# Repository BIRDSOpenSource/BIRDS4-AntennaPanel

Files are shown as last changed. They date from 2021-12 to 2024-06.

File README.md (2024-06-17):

<div align="center">
  <a href="https://lean-sat.org/opensource/">
  
  </a>
</div>

 


# BIRDS4-AntennaPanel
 Documentation for the Antenna Panel used in the BIRDS4 satellite.

Inside the different folders are the Eagle files used in different satellites of the BIRDS 4 generation. Differences are mainly aesthetic (ie. logos and such).

## About the BIRDS4 Program:

The Mission Statement of the Project is:

> “By successfully building and operating first satellite of nation, advance toward indigenous space program in each country”

The project is led by Kyushu Institute of Technology in Japan and involves students from Philippines, Paraguay, Nepal, Turkey and Japan.

Satellite Names: Tsuru (Japan), Guarani-1 (Paraguay) and Maya-2 (Phillipines)

Stakeholders:  Paraguayan Space Agency, Polytechnic Faculty of National University of Asuncion, and Kyushu Institute of Technology (Kyutech) for Japan.

Project duration: 2018-2022

CubeSat: 1U (10x10x10) cm3

Weight: 1.13kg

Launch Date: 21st February 2021 

BIRDS-4 has 1 main missions in total; APRS Store and forward mission

## Organisation structure

```bash

├── .gitattributes
├── AntennaPanel_Partslist.xlsx
├── FM_GuaraniSat
│   ├── BIRDS4_-Y_panel_FM_GUARANI_v3.brd
│   └── BIRDS4_-Y_panel_FM_GUARANI_v3.sch
├── FM_MAYA-2
│   ├── BIRDS4_-Y_panel_FM_MAYA-2_v6.brd
│   └── BIRDS4_-Y_panel_FM_MAYA-2_v6.sch
├── FM_TSURU
│   ├── BIRDS4_-Y_panel_FM_TSURU_v2.brd
│   └── BIRDS4_-Y_panel_FM_TSURU_v2.sch
├── LICENSE
├── README.md
├── mount_bottom.pdf
└── mount_top.pdf

```
> [!CAUTION]
> The files `.sch` and `.brd` files in this repositiry were created using Eagle software.
 
For those that want to import these files into 
KiCAD7 [here's how you do it](https://community.element14.com/technologies/open-source-hardware/b/blog/posts/working-with-kicad-7-importing-eagle-files) 
 or KiCAD5.1 [here's how you do it](https://www.youtube.com/watch?v=RBc02MwpKxk&t=1s).

## Features

## I like this project, can I help you?
You are welcome 🙂

* Give us a star ⭐
* Watch repository to be notified about updates 👀
* If you will find some errors, report them in Issues 🐞
* Try Birds designs on some real computer and let us know how it worked in Discussions. 💬
* We would greatly appreciate if you would also tell others about this ecosystem, it helps us to improve BIRDS Open Source. Thank you!

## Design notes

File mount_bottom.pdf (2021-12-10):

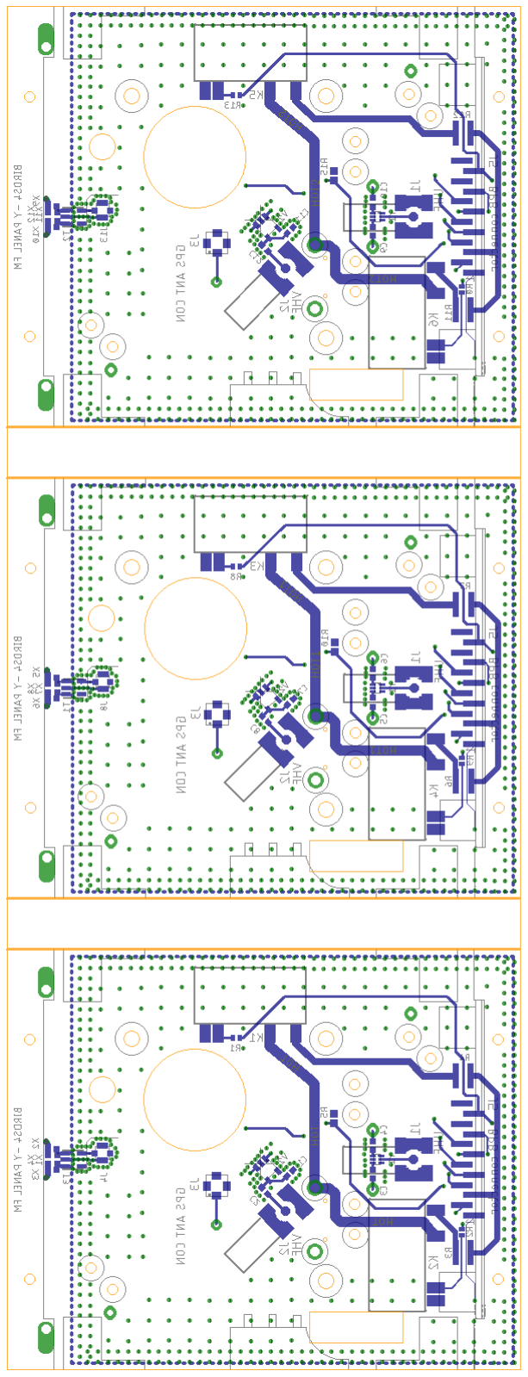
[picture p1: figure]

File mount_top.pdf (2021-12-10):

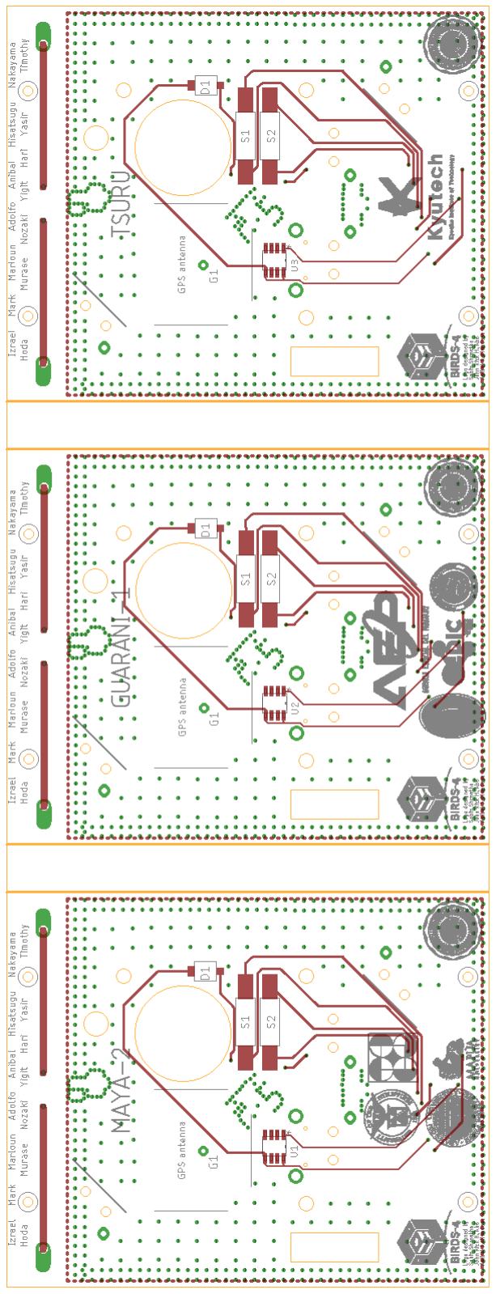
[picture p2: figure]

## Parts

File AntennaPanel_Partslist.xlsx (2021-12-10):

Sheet: 必ずお読みください
入力項目説明
メ ー カ ー |  |  | 電子部品のメーカー名をご入力ください。
部 品 種 別 |  |  | 電子部品の種別をご入力ください。例：チップ抵抗、トランジスタ、LED、など
電 子 部 品 型 番 |  |  | 電子部品の型番をご入力ください。 ※誤表記による不具合を回避するためにも正確なご入力をお願い致します。 ※表面実装の抵抗やコンデンサ(電解、タンタル以外)は、後述「電子部品見取り表」をご参照のうえ、ご入力ください。
配 置 記 号 / リファレンス |  |  | シルク図/配置図に表記された配置記号/リファレンス番号をご入力ください。 ※複数入力する場合は、カンマ「,」区切りでのご入力をお願い致します。 (入力例)R1～R5、R1-5と略さず、R1,R2,R3,R4,R5とご入力ください。 ※電子部品型番ベースでのご記入をお願い致します。（１つの電子部品型番に対して、配置番号を複数記入）
個 数 |  |  | 電子部品の個数をご入力ください。
ピ ン 数 |  |  | 電子部品の総ピン数をご入力ください。 ※基板取付穴、部品取付穴、全てのスルー・ノンスルーホール、面実装部品のパッド、及び次の①～⑤の配線を伴う箇所（①テストピン、②チェックランド、③引き出しランド、④ジャンパピン、⑤入出力ランドの総計。
実装 / 未実装 |  |  | 実装サービスでの「実装」/「未実装」をご選択ください。 ※同じ電子部品型番の中で実装と未実装が分かれる場合は、それぞれ2行に分けて配置記号をご入力ください。
部品分類 | SMD |  | 表面実装部品
 | DIP |  | 挿入部品
 | 特殊 BGA等 |  | BGA/CSP/LGA/QFNなど部品極性が部品の真下に配置された部品 -BGA：Ball Grid Array/下面に半田ボールの端子を配置したパッケージ。 -CSP：Chip Size Package/チッププサイズと同じか、もしくは僅かに大きいパッケージ。 -LGA：Land Grid Array/裏面に外部入出力用のランドを設けたパッケージ。※BGAの半田ボールがない。 -QFN：Quad Flat Non-Lead Package/QFPに似ていますが、外部入出力用のピンが出ていないパッケージ。
P板.com提供部品 (無料) |  |  | 【無償提供部品一覧】シートに記載されている「メーカー型番」を【部品リスト入力フォーム】シートのD列（電子部品型番）に入力し、I列（実装／未実装）を「実装」に設定いただくと、自動的に「○」が表示されます。 ※無料提供部品：チップコンデンサ/チップ抵抗を約1000種、実装サービスをご利用のお客様に無料提供いたします。 ※「○」が付かない場合は全半角の不一致などにより誤判定されている可能性があります。【無償提供部品一覧】シートより型番をコピー＆ペーストにて【部品リスト入力フォーム】にご入力ください。
 |  |  | http://www.p-ban.com/implementation/chip.html
P板.com調達部品(有料） |  |  | P板.com実装サービスで部品調達を希望される場合に○をご選択ください。 ※調達費用のお見積もりは、部品リストの返却と同時にご連絡いたします。 ※ご希望の納期や市場在庫状況によっては、調達が不可となる部品もございますので、予めご了承ください。
パッケージ情報 部品外形/部品仕様 |  |  | 電子部品のパッケージ情報をご入力ください。例：1608 , DIP , 0.5mmピッチQFP , 0.4mmピッチCN
コ メ ン ト |  |  | 特別なご指示のある電子部品について、自由にご入力ください。 例：未実装挿入穴のマスク処理が必要、など
版、変更履歴 |  |  | 部品種毎に、変更履歴を記載してください。 版は、アカウント登録の版に合わせて記載ください。
調達型式、代替型式 |  |  | 無料提供部品の在庫切れや、正確な調達型式を記載いたします。
部品名称見取り表
1.チップ部品（抵抗、コンデンサ）
 |  |  |  |  | 単位：ｍｍ
 |  |  | 電子部品型番 (C:コンデンサ、R:抵抗） | Ａ寸法 | Ｂ寸法
 |  |  | C/R1608 | 1.6 | 0.8
 |  |  | C/R2125 | 2 | 1.25
 |  |  | C/R3216 | 3.2 | 1.6
 |  |  | C/R3225 | 3.2 | 2.5
 |  |  | C/R4532 | 4.5 | 3.2
2.チップタンタルコンデンサ
 |  |  |  |  | 単位：ｍｍ
 |  |  | 電子部品型番 | Ａ寸法 | Ｂ寸法
 |  |  | CT3216 | 3.2 | 1.6
 |  |  | CT3528 | 3.5 | 2.8
 |  |  | CT4726 | 4.7 | 2.6
 |  |  | CT6032 | 6 | 3.2
 |  |  | CT5846 | 5.8 | 4.6
 |  |  | CT7343 | 7.3 | 4.3
3.チップアルミ電解コンデンサ
 |  |  |  |  |  | 単位：ｍｍ
 |  |  | 電子部品型番 | Ａ寸法 | Ｂ寸法 | C寸法
 |  |  | CE33 | 3.3 | 3.3 | φ3.0
 |  |  | CE43 | 4.3 | 4.3 | φ4.0
 |  |  | CE53 | 5.3 | 5.3 | φ5.0
 |  |  | CE66 | 6.6 | 6.6 | φ6.3
 |  |  | CE83 | 8.3 | 8.3 | φ8.0
 |  |  | CE103 | 10.3 | 10.3 | φ10.0
部品取り付け穴は、ピン数に含めてください。
コネクタの場合 |  |  |  |  |  | トランスの場合
部品リストフォーマット変更履歴
2014-02-01 | v2.0 | 松森 | 部品種別の総計を、直接関数に変更
 |  |  | ピン数合計、実装数合計数量を、直接関数に変更
 |  |  | 部品調達見積欄を修正
2014-03-11 | v2.1 | 松森 | *N列、O列が下の方、"○"選択リスト消えていたのを追加
 |  |  | *縮小しても解像度崩れず文字表示するため、フォントを"Meiryo UI"(Windows 標準添付)に変更
 |  |  | *136行目以降を非表示
 |  |  | *"X"列にリストを埋め込み
2014-06-12 | v2.2 | 松森 | *固定行を変更
 |  |  | *在庫状況列に条件付き書式設定
 |  |  | *その他各種バグ修正
2015-03-31 | V2.3 | 松森 | *無償提供部品を記載すると、無償提供部品欄に自動で"○"が表示されるよう条件式を挿入
 |  |  | *併せて、無償提供部品参照用一覧シートの作成・追加
 |  |  | *最小購入数が必要数量を下回る場合、セルを赤色にハッチングする
 |  |  | *シート1の名称変更
 |  |  | *変更履歴シートの追加
2015-06-19 | v2.4 | 松森 | ・ゼロΩ抵抗を無償対象に追加
 |  |  | ・変更履歴の列を追加し、変更履歴シートを削除
 |  |  | ・その他書式、印刷機能の変更
 |  |  | ・無償提供部品の入れ替え
2015-08-14 | v2.5 | 松森 | ・ゼロΩ抵抗の無償対象品が正しく反映されていなかったバグ修正
 |  |  | ・フォームへバージョン情報を埋め込み
2015-11-05 | v2.6 | 上田 | ・無償提供部品(RK73H2ATTD1601F)の抵抗値を正しい値に修正
2015-11-09 | v2.7 | 上田 | ・P板.com調達部品(無料)欄のフォントを変更
2016-01-15 | v2.8 | 箕浦 | ・無償提供部品一覧の「GRM32NF11E106Z」を削除
 |  |  | ・部品リスト入力フォームの4行目F列～L列の計算式が136行目以降を対象としていなかった不具合を修正
2016-01-27 | v2.9 | 箕浦 | ・「無償提供部品一覧」シートの表記修正
2016-08-26 | v2.10 | 松森 | ・「GRM31CF11E106Z」の許容差値修正
2016-11-15 | v2.11 | 松森 | ・部品調達欄表示順序変更
 |  |  | ・備考欄、荷姿欄追加
 |  |  | ・在庫状況のリスト微修正
2017-03-21 | v2.12 | 松森 | ・調達金額合計欄作成
 |  |  | ・在庫状況「長納期」を追加
 |  |  | ・その他微修正
2017-06-29 | v2.13 | 松森 | ・村田製3216サイズ以上のチップコンの取扱い中止
2017-07-19 | V2.14 | 松森 | ・KOA製1005サイズの定格電力を0.1Wに変更
 |  |  | (2015年10月のKOA仕様変更に伴う)
2017-09-14 | v2.15 | 松森 | ・KOA製2012サイズの定格電力を0.25Wへ変更
 |  |  | ・KOA製1608サイズ、1K以下の定格電力を0.125Wへ変更
 |  |  | ・MURATA製一部型式、許容差および定格修正
 |  |  | ・MURATA製一部部品削除
 |  |  | ・その他書式設定等微修正
2017-10-12 | v2.20 | 松森 | ・部品調達関連項目の移動
 |  |  | ・条件付き書式追加
2018-06-22 | v2.31 | 松森 | ・「1608」サイズと「2012」サイズのチップコンデンサを無償対象品から除外
2018-10-18 | V2.32 | 山田 | ・部品調達関連項目追加（条件付き書式追加/在庫状況：在庫少追加）
 |  |  | ・「必ずお読みください」シートの「配置記号 / リファレンス」の項目修正（配置記号の省略について）

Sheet: 部品リスト入力フォーム
Ver.2.32 |  |  | 電 子 部 品 型 番 ※半角英数字 ※サフィックスまで入力必須 | 配 置 記 号 リ フ ァ レ ン ス ※半角英数字） | 個数 | ピ ン 数 (部品取付穴 を含む） |  | 実装/ 未実装 | 部 品 分 類 |  |  | 必要数 実装枚数を入れてください。 ↓ | P板.com 提供 部品 (無料) | P板.com 調達 部品 (有料） | パッケージ情報 部品外形/部品仕様 | コ メ ン ト ※未実装挿入穴のマスク 処理が必要、など | 版 変更履歴 | 入荷数 | 返却
No | メーカー | 部品種別 |  |  |  | 1個 あたり | 合計 | 実装個数 | SMD | DIP | 特殊 BGA等 |  |  |  |  |  |  |  |  | P板.com部品調達使用欄
 |  |  |  |  | 21 | 65 | 78 | 21 | 19 | 0 | 2 | 6 | リスト (http://www.p-ban.com/implementation/chip.html)
1 □ | Panasonic Electric Works | PhtoMOS | AQZ102 | K1,K2 | 2 | 4 | 8 | 実装 | SMD |  |  | 12 |  |  | 4-SIP |  |  |  | □
2 □ | Vishay Dale | RESISTOR RES SMD 1 OHM 1% 1.5W 1218 | CRCW12181R00FKEKHP | R3,R4 | 2 | 2 | 4 | 実装 | SMD |  |  | 12 |  |  | 1218/3246 |  |  |  | □
3 □ | Analog Devices Inc. | SENSOR TEMP ANLG VOLT 8-SOIC | TMP36FSZ-REEL | U1 | 1 | 8 | 8 | 実装 | SMD |  |  | 6 |  |  | 8-SOIC (0.154", 3.90mm Width) |  |  |  | □
4 □ | KOA | チップ抵抗 | RK73H1ETTP1001F | R1,R2 | 2 | 2 | 4 | 実装 | SMD |  |  | 12 | ○ |  | 1005 |  |  |  | □
5 □ | Mini-Circuits | Balun 1:1.5 | NCS1.5-232+ | T1 | 1 | 6 | 6 | 実装 | SMD |  |  | 6 |  |  |  |  |  |  | □
6 □ | M/A-Com Technology Solutions Series | Balun 1:1 | MABA-010245-CT1160 | T2 | 1 | 5 | 5 | 実装 | SMD |  |  | 6 |  |  |  |  |  |  | □
7 □ | Amphenol RF Division | CONN MMCX JACK STR 50 OHM | 908-22101T | J3 | 1 | 4 | 4 | 実装 | SMD |  |  | 6 |  |  |  |  |  |  | □
8 □ | Cinch Connectivity Solutions Johnson | CONN SMA JACK R/A 50 OHM | 142-0711-301 | J1,J2 | 2 | 3 | 6 | 実装 | 特殊（BGA等） |  |  | 12 |  |  | Bulk |  |  |  | □
9 □ | Johanson Technology Inc. | キャパシタ 18pF | S603DS | C3,C4 | 2 | 2 | 4 | 実装 | SMD |  |  | 12 |  |  | 603 |  |  |  | □
10 □ | Johanson Technology Inc. | キャパシタ 82pF | S603DS | C2 | 1 | 2 | 2 | 実装 | SMD |  |  | 6 |  |  | 603 |  |  |  | □
11 □ | Johanson Technology Inc. | インダクタ 220nH | L603DC | C1 | 1 | 2 | 2 | 実装 | SMD |  |  | 6 |  |  | 603 |  |  |  | □
12 □ | 廣杉計器 | コネクタ | FSM-21045-12 | J5 | 1 | 12 | 12 | 実装 | SMD |  |  | 6 |  |  | FSM-21045-12 |  |  |  | □
13 □ | Hirose Electric Co Ltd | RF connector | U.FL-R-SMT(01) | J4 | 1 | 4 | 4 | 実装 | SMD |  |  | 6 |  |  |  |  |  |  | □
14 □ | Mini-Circuits | Balun 1:1 | TC1-1T+ | T3 | 1 | 5 | 5 | 実装 | SMD |  |  | 6 |  |  |  |  |  |  | □
15 □ | osram opto semiconductors | photodiode sensor | SFH 2430-Z | D1 | 1 | 2 | 2 | 実装 | SMD |  |  | 6 |  |  |  |  |  |  | □
16 □ | KOA | 3kohm resistor | RK73H1JTTD3001F | R5 | 1 | 2 | 2 | 実装 | SMD |  |  | 6 | ○ |  |  |  |  |  | □
18 □ |  |  |  |  |  |  |  |  |  |  |  |  |  |  |  |  |  |  | □
19 □ |  |  |  |  |  |  |  |  |  |  |  |  |  |  |  |  |  |  | □
20 □ |  |  |  |  |  |  |  |  |  |  |  |  |  |  |  |  |  |  | □
21 □ |  |  |  |  |  |  |  |  |  |  |  |  |  |  |  |  |  |  | □
22 □ |  |  |  |  |  |  |  |  |  |  |  |  |  |  |  |  |  |  | □
23 □ |  |  |  |  |  |  |  |  |  |  |  |  |  |  |  |  |  |  | □
24 □ |  |  |  |  |  |  |  |  |  |  |  |  |  |  |  |  |  |  | □
25 □ |  |  |  |  |  |  |  |  |  |  |  |  |  |  |  |  |  |  | □
26 □ |  |  |  |  |  |  |  |  |  |  |  |  |  |  |  |  |  |  | □
27 □ |  |  |  |  |  |  |  |  |  |  |  |  |  |  |  |  |  |  | □
28 □ |  |  |  |  |  |  |  |  |  |  |  |  |  |  |  |  |  |  | □
29 □ |  |  |  |  |  |  |  |  |  |  |  |  |  |  |  |  |  |  | □
30 □ |  |  |  |  |  |  |  |  |  |  |  |  |  |  |  |  |  |  | □
31 □ |  |  |  |  |  |  |  |  |  |  |  |  |  |  |  |  |  |  | □
32 □ |  |  |  |  |  |  |  |  |  |  |  |  |  |  |  |  |  |  | □
33 □ |  |  |  |  |  |  |  |  |  |  |  |  |  |  |  |  |  |  | □
34 □ |  |  |  |  |  |  |  |  |  |  |  |  |  |  |  |  |  |  | □
35 □ |  |  |  |  |  |  |  |  |  |  |  |  |  |  |  |  |  |  | □
36 □ |  |  |  |  |  |  |  |  |  |  |  |  |  |  |  |  |  |  | □
37 □ |  |  |  |  |  |  |  |  |  |  |  |  |  |  |  |  |  |  | □
38 □ |  |  |  |  |  |  |  |  |  |  |  |  |  |  |  |  |  |  | □
39 □ |  |  |  |  |  |  |  |  |  |  |  |  |  |  |  |  |  |  | □
40 □ |  |  |  |  |  |  |  |  |  |  |  |  |  |  |  |  |  |  | □
41 □ |  |  |  |  |  |  |  |  |  |  |  |  |  |  |  |  |  |  | □
42 □ |  |  |  |  |  |  |  |  |  |  |  |  |  |  |  |  |  |  | □
43 □ |  |  |  |  |  |  |  |  |  |  |  |  |  |  |  |  |  |  | □
44 □ |  |  |  |  |  |  |  |  |  |  |  |  |  |  |  |  |  |  | □
45 □ |  |  |  |  |  |  |  |  |  |  |  |  |  |  |  |  |  |  | □
46 □ |  |  |  |  |  |  |  |  |  |  |  |  |  |  |  |  |  |  | □
47 □ |  |  |  |  |  |  |  |  |  |  |  |  |  |  |  |  |  |  | □
48 □ |  |  |  |  |  |  |  |  |  |  |  |  |  |  |  |  |  |  | □
49 □ |  |  |  |  |  |  |  |  |  |  |  |  |  |  |  |  |  |  | □
50 □ |  |  |  |  |  |  |  |  |  |  |  |  |  |  |  |  |  |  | □
51 □ |  |  |  |  |  |  |  |  |  |  |  |  |  |  |  |  |  |  | □
52 □ |  |  |  |  |  |  |  |  |  |  |  |  |  |  |  |  |  |  | □
53 □ |  |  |  |  |  |  |  |  |  |  |  |  |  |  |  |  |  |  | □
54 □ |  |  |  |  |  |  |  |  |  |  |  |  |  |  |  |  |  |  | □
55 □ |  |  |  |  |  |  |  |  |  |  |  |  |  |  |  |  |  |  | □
56 □ |  |  |  |  |  |  |  |  |  |  |  |  |  |  |  |  |  |  | □
57 □ |  |  |  |  |  |  |  |  |  |  |  |  |  |  |  |  |  |  | □
58 □ |  |  |  |  |  |  |  |  |  |  |  |  |  |  |  |  |  |  | □
59 □ |  |  |  |  |  |  |  |  |  |  |  |  |  |  |  |  |  |  | □
60 □ |  |  |  |  |  |  |  |  |  |  |  |  |  |  |  |  |  |  | □
61 □ |  |  |  |  |  |  |  |  |  |  |  |  |  |  |  |  |  |  | □
62 □ |  |  |  |  |  |  |  |  |  |  |  |  |  |  |  |  |  |  | □
63 □ |  |  |  |  |  |  |  |  |  |  |  |  |  |  |  |  |  |  | □
64 □ |  |  |  |  |  |  |  |  |  |  |  |  |  |  |  |  |  |  | □
65 □ |  |  |  |  |  |  |  |  |  |  |  |  |  |  |  |  |  |  | □
66 □ |  |  |  |  |  |  |  |  |  |  |  |  |  |  |  |  |  |  | □
67 □ |  |  |  |  |  |  |  |  |  |  |  |  |  |  |  |  |  |  | □
68 □ |  |  |  |  |  |  |  |  |  |  |  |  |  |  |  |  |  |  | □
69 □ |  |  |  |  |  |  |  |  |  |  |  |  |  |  |  |  |  |  | □
70 □ |  |  |  |  |  |  |  |  |  |  |  |  |  |  |  |  |  |  | □
71 □ |  |  |  |  |  |  |  |  |  |  |  |  |  |  |  |  |  |  | □
72 □ |  |  |  |  |  |  |  |  |  |  |  |  |  |  |  |  |  |  | □
73 □ |  |  |  |  |  |  |  |  |  |  |  |  |  |  |  |  |  |  | □
74 □ |  |  |  |  |  |  |  |  |  |  |  |  |  |  |  |  |  |  | □
75 □ |  |  |  |  |  |  |  |  |  |  |  |  |  |  |  |  |  |  | □
76 □ |  |  |  |  |  |  |  |  |  |  |  |  |  |  |  |  |  |  | □
77 □ |  |  |  |  |  |  |  |  |  |  |  |  |  |  |  |  |  |  | □
78 □ |  |  |  |  |  |  |  |  |  |  |  |  |  |  |  |  |  |  | □
79 □ |  |  |  |  |  |  |  |  |  |  |  |  |  |  |  |  |  |  | □
80 □ |  |  |  |  |  |  |  |  |  |  |  |  |  |  |  |  |  |  | □
81 □ |  |  |  |  |  |  |  |  |  |  |  |  |  |  |  |  |  |  | □
82 □ |  |  |  |  |  |  |  |  |  |  |  |  |  |  |  |  |  |  | □
83 □ |  |  |  |  |  |  |  |  |  |  |  |  |  |  |  |  |  |  | □
84 □ |  |  |  |  |  |  |  |  |  |  |  |  |  |  |  |  |  |  | □
85 □ |  |  |  |  |  |  |  |  |  |  |  |  |  |  |  |  |  |  | □
86 □ |  |  |  |  |  |  |  |  |  |  |  |  |  |  |  |  |  |  | □
87 □ |  |  |  |  |  |  |  |  |  |  |  |  |  |  |  |  |  |  | □
88 □ |  |  |  |  |  |  |  |  |  |  |  |  |  |  |  |  |  |  | □
89 □ |  |  |  |  |  |  |  |  |  |  |  |  |  |  |  |  |  |  | □
90 □ |  |  |  |  |  |  |  |  |  |  |  |  |  |  |  |  |  |  | □
91 □ |  |  |  |  |  |  |  |  |  |  |  |  |  |  |  |  |  |  | □
92 □ |  |  |  |  |  |  |  |  |  |  |  |  |  |  |  |  |  |  | □
93 □ |  |  |  |  |  |  |  |  |  |  |  |  |  |  |  |  |  |  | □
94 □ |  |  |  |  |  |  |  |  |  |  |  |  |  |  |  |  |  |  | □
95 □ |  |  |  |  |  |  |  |  |  |  |  |  |  |  |  |  |  |  | □
96 □ |  |  |  |  |  |  |  |  |  |  |  |  |  |  |  |  |  |  | □
97 □ |  |  |  |  |  |  |  |  |  |  |  |  |  |  |  |  |  |  | □
98 □ |  |  |  |  |  |  |  |  |  |  |  |  |  |  |  |  |  |  | □
99 □ |  |  |  |  |  |  |  |  |  |  |  |  |  |  |  |  |  |  | □
100 □ |  |  |  |  |  |  |  |  |  |  |  |  |  |  |  |  |  |  | □
101 □ |  |  |  |  |  |  |  |  |  |  |  |  |  |  |  |  |  |  | □
102 □ |  |  |  |  |  |  |  |  |  |  |  |  |  |  |  |  |  |  | □
103 □ |  |  |  |  |  |  |  |  |  |  |  |  |  |  |  |  |  |  | □
104 □ |  |  |  |  |  |  |  |  |  |  |  |  |  |  |  |  |  |  | □
105 □ |  |  |  |  |  |  |  |  |  |  |  |  |  |  |  |  |  |  | □
106 □ |  |  |  |  |  |  |  |  |  |  |  |  |  |  |  |  |  |  | □
107 □ |  |  |  |  |  |  |  |  |  |  |  |  |  |  |  |  |  |  | □
108 □ |  |  |  |  |  |  |  |  |  |  |  |  |  |  |  |  |  |  | □
109 □ |  |  |  |  |  |  |  |  |  |  |  |  |  |  |  |  |  |  | □
110 □ |  |  |  |  |  |  |  |  |  |  |  |  |  |  |  |  |  |  | □
111 □ |  |  |  |  |  |  |  |  |  |  |  |  |  |  |  |  |  |  | □
112 □ |  |  |  |  |  |  |  |  |  |  |  |  |  |  |  |  |  |  | □
113 □ |  |  |  |  |  |  |  |  |  |  |  |  |  |  |  |  |  |  | □
114 □ |  |  |  |  |  |  |  |  |  |  |  |  |  |  |  |  |  |  | □
115 □ |  |  |  |  |  |  |  |  |  |  |  |  |  |  |  |  |  |  | □
116 □ |  |  |  |  |  |  |  |  |  |  |  |  |  |  |  |  |  |  | □
117 □ |  |  |  |  |  |  |  |  |  |  |  |  |  |  |  |  |  |  | □
118 □ |  |  |  |  |  |  |  |  |  |  |  |  |  |  |  |  |  |  | □
119 □ |  |  |  |  |  |  |  |  |  |  |  |  |  |  |  |  |  |  | □
120 □ |  |  |  |  |  |  |  |  |  |  |  |  |  |  |  |  |  |  | □
121 □ |  |  |  |  |  |  |  |  |  |  |  |  |  |  |  |  |  |  | □
122 □ |  |  |  |  |  |  |  |  |  |  |  |  |  |  |  |  |  |  | □
123 □ |  |  |  |  |  |  |  |  |  |  |  |  |  |  |  |  |  |  | □
124 □ |  |  |  |  |  |  |  |  |  |  |  |  |  |  |  |  |  |  | □
125 □ |  |  |  |  |  |  |  |  |  |  |  |  |  |  |  |  |  |  | □
126 □ |  |  |  |  |  |  |  |  |  |  |  |  |  |  |  |  |  |  | □
127 □ |  |  |  |  |  |  |  |  |  |  |  |  |  |  |  |  |  |  | □
128 □ |  |  |  |  |  |  |  |  |  |  |  |  |  |  |  |  |  |  | □
129 □ |  |  |  |  |  |  |  |  |  |  |  |  |  |  |  |  |  |  | □
130 □ |  |  |  |  |  |  |  |  |  |  |  |  |  |  |  |  |  |  | □
131 □ |  |  |  |  |  |  |  |  |  |  |  |  |  |  |  |  |  |  | □
132 □ |  |  |  |  |  |  |  |  |  |  |  |  |  |  |  |  |  |  | □
133 □ |  |  |  |  |  |  |  |  |  |  |  |  |  |  |  |  |  |  | □
134 □ |  |  |  |  |  |  |  |  |  |  |  |  |  |  |  |  |  |  | □
135 □ |  |  |  |  |  |  |  |  |  |  |  |  |  |  |  |  |  |  | □
136 □ |  |  |  |  |  |  |  |  |  |  |  |  |  |  |  |  |  |  | □
137 □ |  |  |  |  |  |  |  |  |  |  |  |  |  |  |  |  |  |  | □
138 □ |  |  |  |  |  |  |  |  |  |  |  |  |  |  |  |  |  |  | □
139 □ |  |  |  |  |  |  |  |  |  |  |  |  |  |  |  |  |  |  | □
140 □ |  |  |  |  |  |  |  |  |  |  |  |  |  |  |  |  |  |  | □
141 □ |  |  |  |  |  |  |  |  |  |  |  |  |  |  |  |  |  |  | □
142 □ |  |  |  |  |  |  |  |  |  |  |  |  |  |  |  |  |  |  | □
143 □ |  |  |  |  |  |  |  |  |  |  |  |  |  |  |  |  |  |  | □
144 □ |  |  |  |  |  |  |  |  |  |  |  |  |  |  |  |  |  |  | □
145 □ |  |  |  |  |  |  |  |  |  |  |  |  |  |  |  |  |  |  | □
146 □ |  |  |  |  |  |  |  |  |  |  |  |  |  |  |  |  |  |  | □
147 □ |  |  |  |  |  |  |  |  |  |  |  |  |  |  |  |  |  |  | □
148 □ |  |  |  |  |  |  |  |  |  |  |  |  |  |  |  |  |  |  | □
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

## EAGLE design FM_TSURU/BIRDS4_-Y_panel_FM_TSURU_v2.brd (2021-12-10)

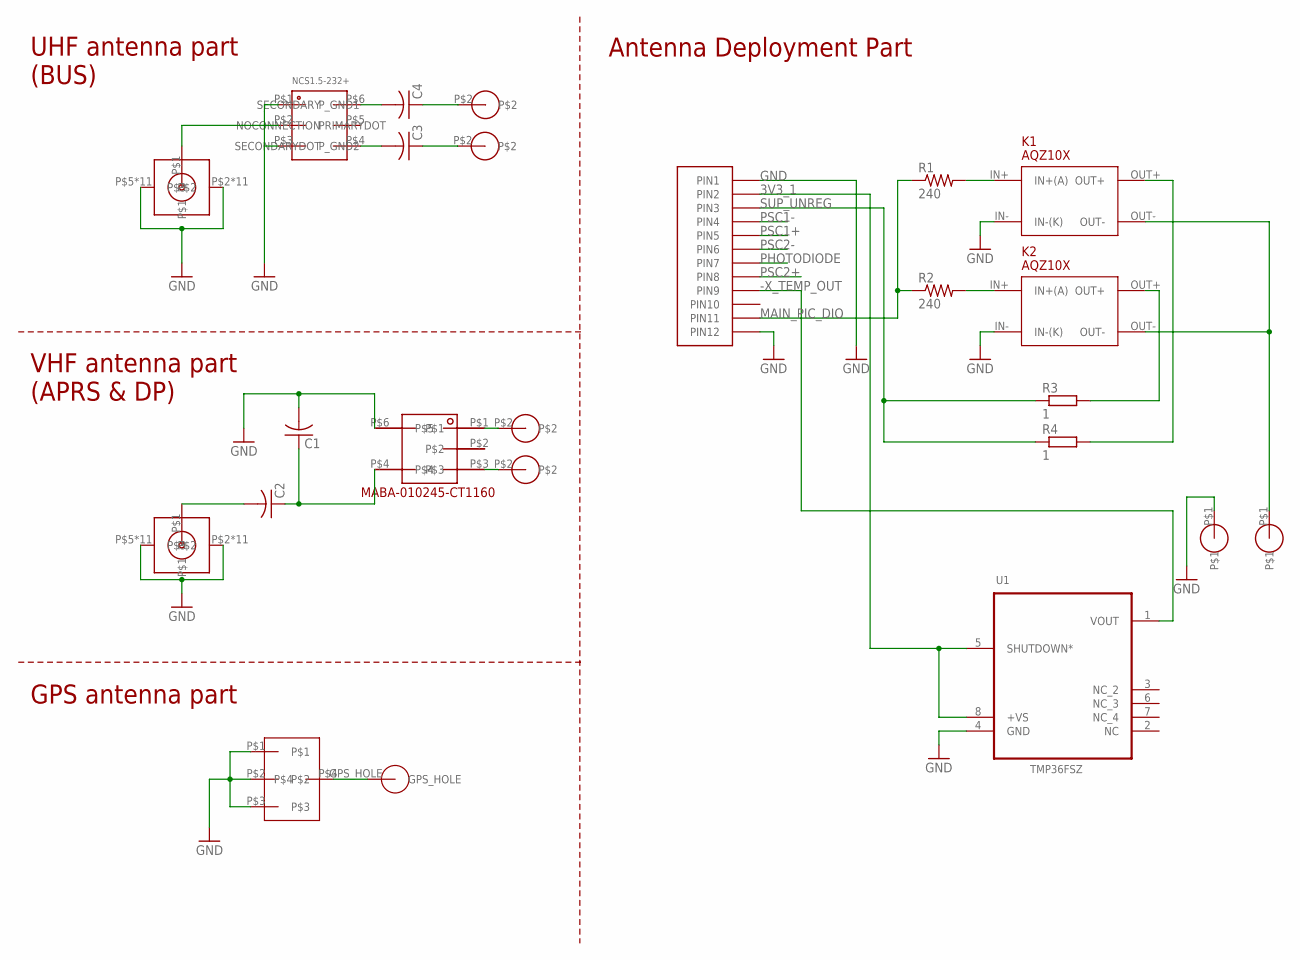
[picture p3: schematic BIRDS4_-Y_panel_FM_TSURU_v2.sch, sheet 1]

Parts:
C1, C2, C3, C4: C-USC1608; C1608
HOLE1, HOLE2: B4_FOR_NEW_DIPOLE
HOLE7: GPS_HOLE
J1, J2: SMA_142_0711_301
J3: MMCX_GPS
J5: HEADER12PIN
K1, K2: AQZ10X
NCS1: NCS1.5-232+
R1, R2: 240; R0402
R3, R4: 1; R1218
U1: TMP36FSZ; SOIC_N
U$1, U$5: NICR_HOLE
U$2: MABA-010245-CT1160
U$3, U$4: B4_FOR_NEW_DIPOLE

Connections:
3V3_1: J5.P2 (PIN2), U1.5 (SHUTDOWN*), U1.8 (+VS); also elsewhere on the board
-X_TEMP_OUT: J5.P9 (PIN9), U1.1 (VOUT)
GND: C1.2, J1.P$2, J1.P$3, J1.P$4, J1.P$5, J1.P$6, J1.P$7, J1.P$8, J1.P$9, J1.P$10, J1.P$11, J1.P$12, J1.P$13, J1.P$14, J1.P$15, J1.P$16, J1.P$17, J1.P$18, J1.P$19, J1.P$20, J1.P$21, J1.P$22, J1.P$23, J2.P$2, J2.P$3, J2.P$4, J2.P$5, J2.P$6, J2.P$7, J2.P$8, J2.P$9, J2.P$10, J2.P$11, J2.P$12, J2.P$13, J2.P$14, J2.P$15, J2.P$16, J2.P$17, J2.P$18, J2.P$19, J2.P$20, J2.P$21, J2.P$22, J2.P$23, J3.P$1, J3.P$2, J3.P$3, J5.P1 (PIN1), J5.P12 (PIN12), K1.IN- (IN-(K)), K2.IN- (IN-(K)), NCS1.P$1 (P_GND1), NCS1.P$3 (P_GND2), U1.4 (GND), U$2.P$6, U$5.P$1; also elsewhere on the board
HOT: K1.OUT-, K2.OUT-, U$1.P$1
MAIN_PIC_DIO: J5.P11 (PIN11), R1.1, R2.1
unnamed: K1.IN+ (IN+(A)), R1.2
unnamed: K1.OUT+, R4.2
unnamed: K2.IN+ (IN+(A)), R2.2
unnamed: C4.1, HOLE2.P$2
unnamed: C2.2, J2.P$1
unnamed: C1.1, C2.1, U$2.P$4
unnamed: U$2.P$1, U$3.P$2
unnamed: U$2.P$3, U$4.P$2
unnamed: C3.1, HOLE1.P$2
unnamed: C4.2, NCS1.P$6 (SECONDARY)
unnamed: C3.2, NCS1.P$4 (SECONDARYDOT)
unnamed: J1.P$1, NCS1.P$2 (PRIMARYDOT)
unnamed: K2.OUT+, R3.2
unnamed: HOLE7.GPS_HOLE, J3.P$4
PHOTODIODE: J5.P7 (PIN7); also elsewhere on the board
PSC1+: J5.P5 (PIN5); also elsewhere on the board
PSC1-: J5.P4 (PIN4); also elsewhere on the board
PSC2+: J5.P8 (PIN8); also elsewhere on the board
PSC2-: J5.P6 (PIN6); also elsewhere on the board
SUP_UNREG: J5.P3 (PIN3), R3.1, R4.1

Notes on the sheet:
UHF antenna part (BUS)
VHF antenna part (APRS & DP)
GPS antenna part
Antenna Deployment Part

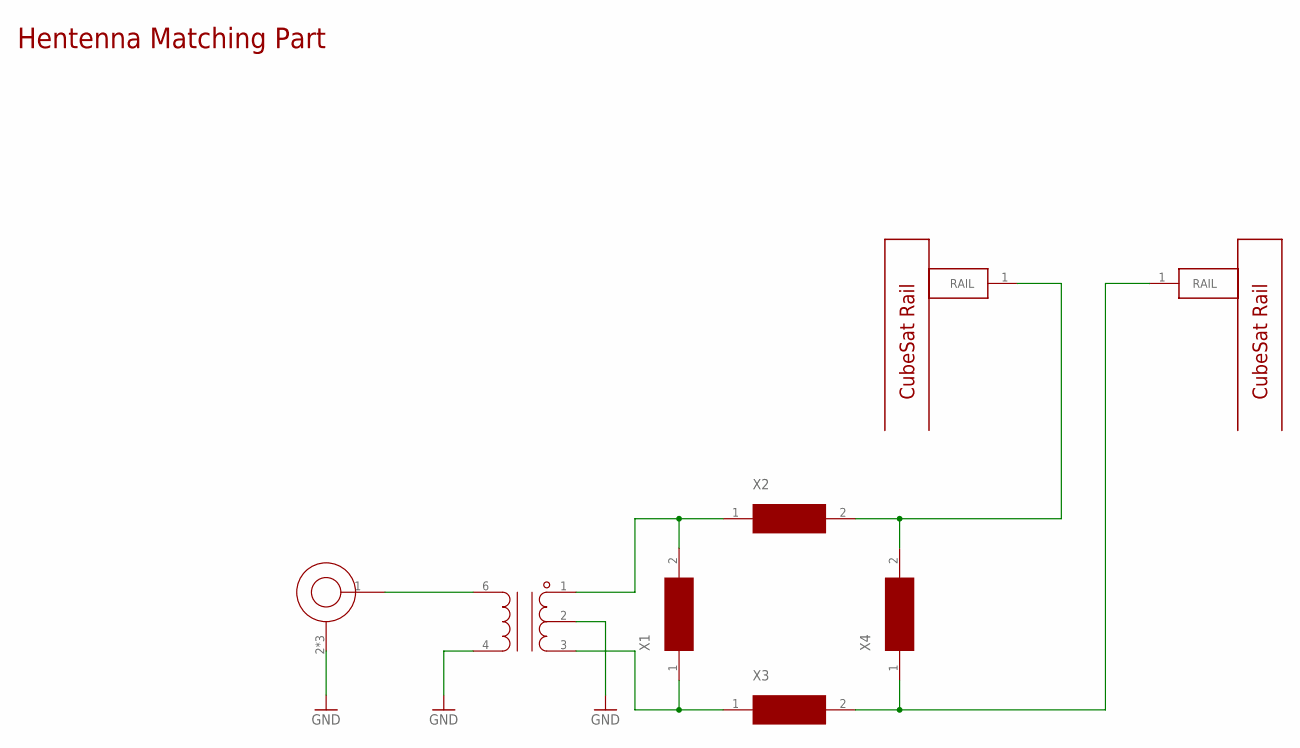
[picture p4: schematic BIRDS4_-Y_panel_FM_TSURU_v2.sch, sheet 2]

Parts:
HOLE8, HOLE9: CUBESAT_RAIL; HOLE
J4: HNT RF CON; R302302000
T3: TC1-1T+; TC1.5-52T+
X1, X2, X3, X4: PASSIVECOMPONENT1608; C1608

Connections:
GND: J4.2 (GND), J4.3 (GND), J4.4 (GND), T3.2, T3.4; also elsewhere on the board
unnamed: T3.1, X1.2, X2.1
unnamed: T3.3, X1.1, X3.1
unnamed: J4.1 (LINE), T3.6
unnamed: HOLE8.1, X2.2, X4.2
unnamed: HOLE9.1, X3.2, X4.1

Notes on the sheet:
Hentenna Matching Part

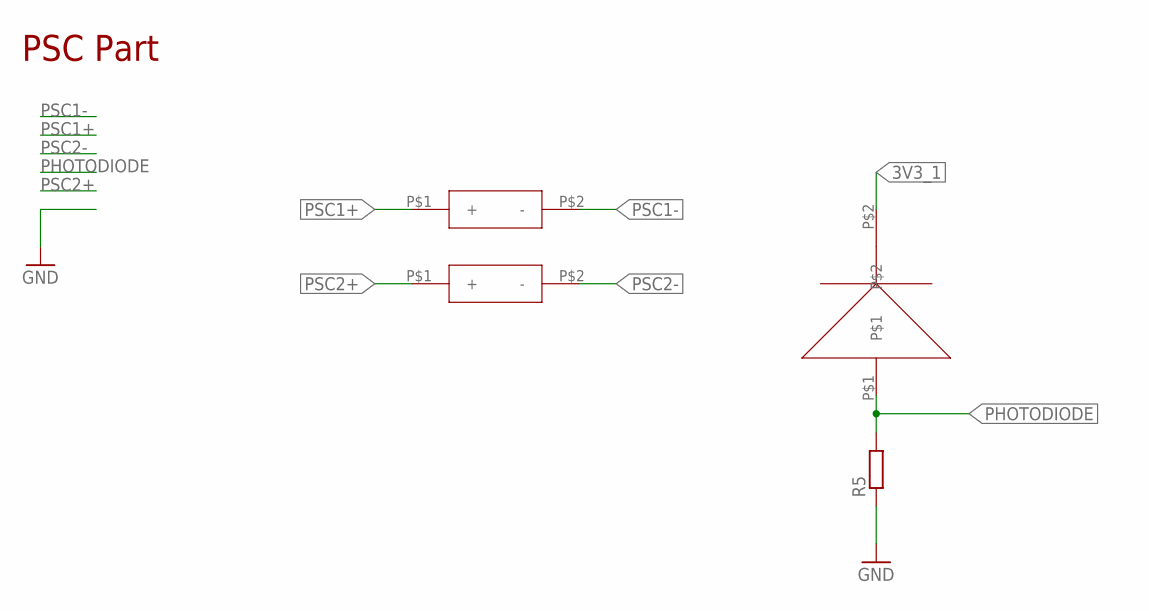
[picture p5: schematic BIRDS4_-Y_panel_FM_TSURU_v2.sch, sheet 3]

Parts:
D1: SFH2430
R5: R-EU_R0805; R0805
S1, S2: PEROVSKITE

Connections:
3V3_1: D1.P$2; also elsewhere on the board
GND: R5.1; also elsewhere on the board
PHOTODIODE: D1.P$1, R5.2; also elsewhere on the board
PSC1+: S1.P$1 (+); also elsewhere on the board
PSC1-: S1.P$2 (-); also elsewhere on the board
PSC2+: S2.P$1 (+); also elsewhere on the board
PSC2-: S2.P$2 (-); also elsewhere on the board

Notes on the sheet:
PSC Part

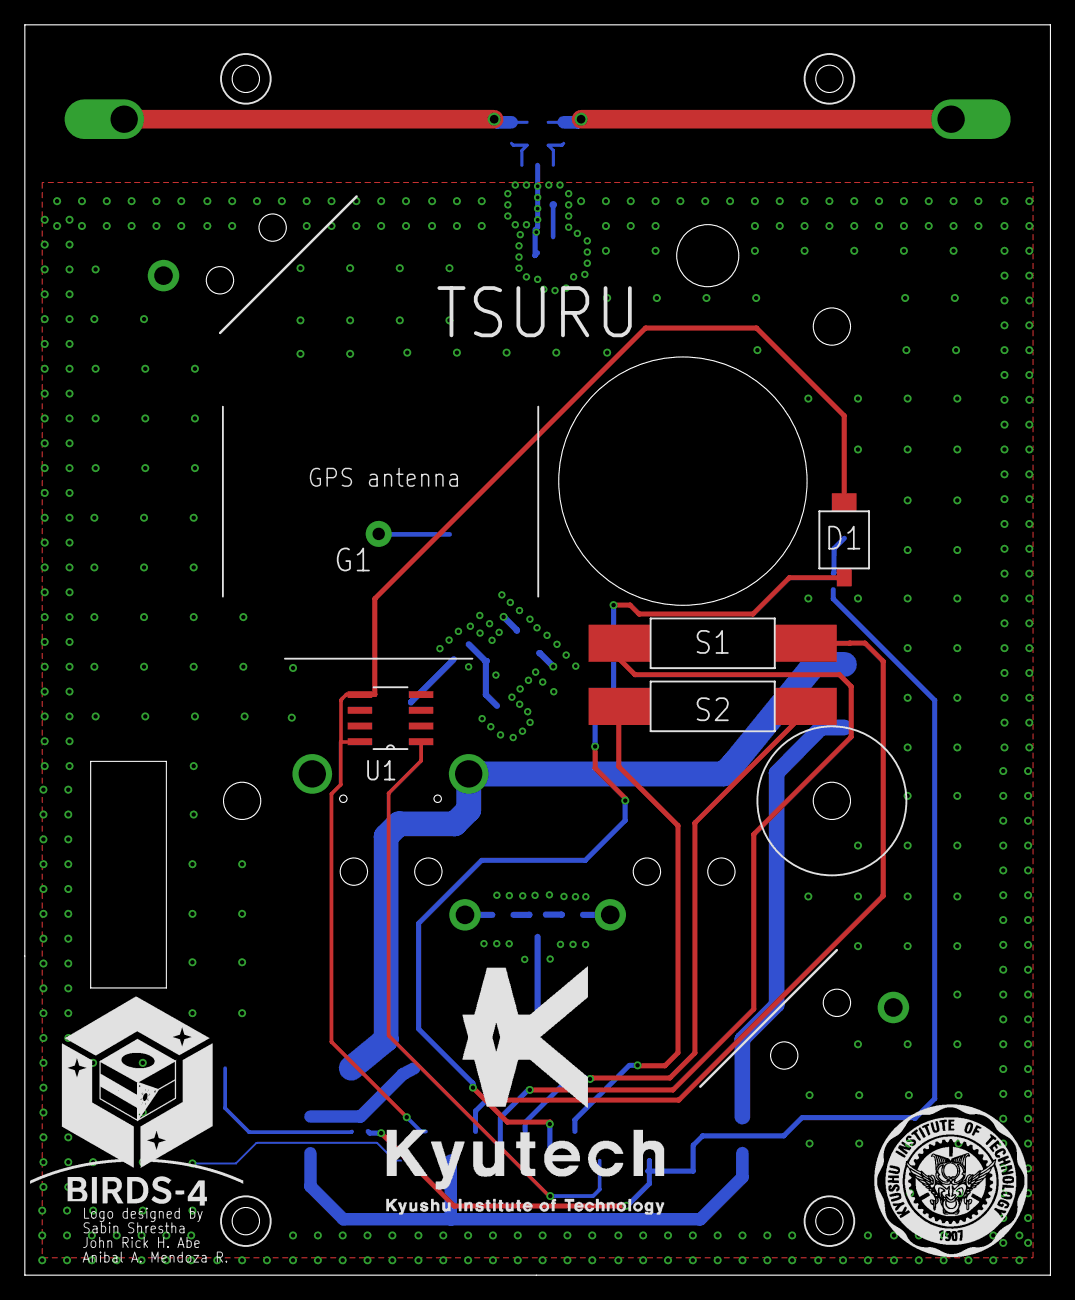
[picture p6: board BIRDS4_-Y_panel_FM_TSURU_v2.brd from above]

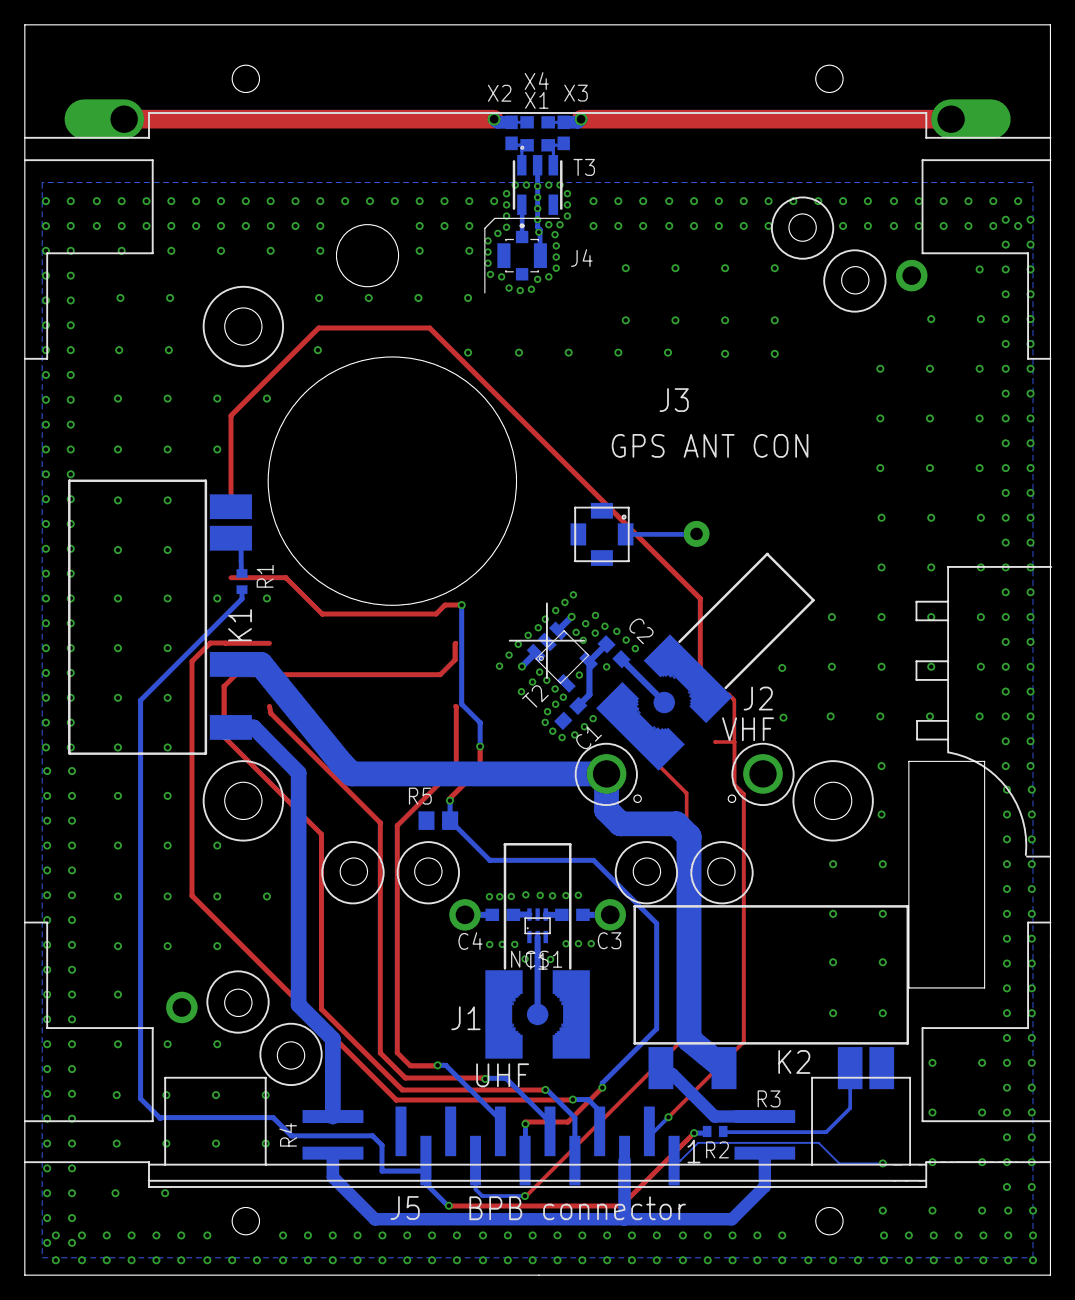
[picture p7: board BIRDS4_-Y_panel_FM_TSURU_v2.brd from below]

Board: 4 copper layers, 82.6 x 100.7 mm, 36 parts (26 on the bottom side), 30 nets.
